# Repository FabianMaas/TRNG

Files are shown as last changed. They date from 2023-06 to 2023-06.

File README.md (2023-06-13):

<!-- markdown project template used: https://github.com/othneildrew/Best-README-Template -->

<!-- PROJECT SHIELDS -->
[][contributors-url]
[][stars-url]
[][issues-url]
[][license-url]

<!-- PROJECT LOGO -->
<br />
<div align="center">
  <a href="https://github.com/FabianMaas/TRNG">
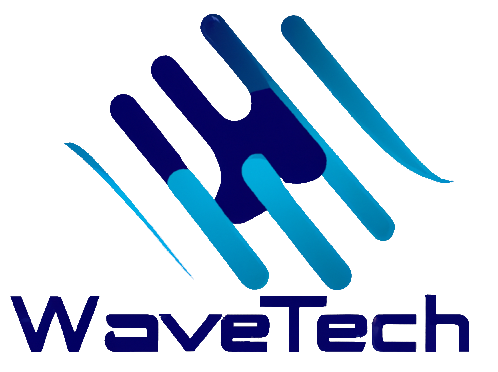
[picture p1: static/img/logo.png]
    
  </a>

<h3 align="center">True Random Number Generator</h3>

  <p align="center">
    An awesome TRNG based on a modified galton board.<br>
    Includes a REST API and a simple frontend.
    <br />
    <a href="https://github.com/FabianMaas/TRNG/tree/main/docs"><strong>Explore the docs »</strong></a>
    <br />
  </p>
</div>

---

<!-- TABLE OF CONTENTS -->
<details open>
  <summary>Table of Contents</summary>
  <ol>
    <li>
      <a href="#mag-about-the-project">About The Project</a>
      <ul>
        <li><a href="#gear-rest-api-endpoints">REST API</a></li>
        <li><a href="#construction_worker_man-built-with">Built With</a></li>
      </ul>
    </li>
    <li>
      <a href="#runner-getting-started">Getting Started</a>
      <ul>
        <li><a href="#pushpin-prerequisites">Prerequisites</a></li>
        <li><a href="#zap-installation">Installation</a></li>
        <li><a href="#white_check_mark-startup-of-the-rest-api">Startup of the api</a></li> 
      </ul>
    </li>
    <li>
      <a href="#camera_flash-screenshots">Screenshots</a>
      <ul>
        <li><a href="#starting-the-system">Starting the system</a></li>
        <li><a href="#generating-random-numbers">Generation</a></li>
        <li><a href="#exporting-the-generated-random-numbers">Export</a></li>
        <li><a href="#switching-to-dark-theme">Dark theme</a></li>
      </ul>
    </li>  
    <li><a href="#construction_worker_man-building-the-galton-board">Building the galton board</a></li>
    <li><a href="#scroll-license">License</a></li>
  </ol>
</details>

---

<!-- ABOUT THE PROJECT -->
## :mag: About The Project

| Bild 1 |  Bild 2 |
|:---:|:---:|

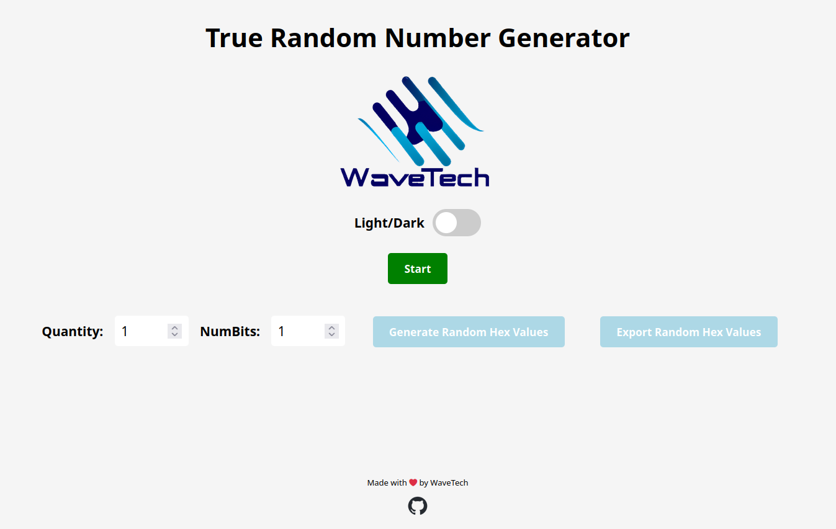
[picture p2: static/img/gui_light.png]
Bild 1


<!-- test 
<div style="display: flex; align-items: center;">
  <img src="static/img/gui_light.png" style="width: 49%;" alt="Beschreibung des Bildes">
  <img src="static/img/gui_dark.png" style="width: 50%; margin-top: auto; margin-bottom: auto;" alt="Beschreibung des Bildes">
</div> 
-->

<br>

The Galton Board is a Physical True Random Number Generator.<br>
The goal is to generate random numbers that can be used for cryptographic processes.<br>
It is based on a physical noise source and generates random numbers that fulfill the required PTG.2 standard of the
Federal Office for Information Security (BSI).<br>
<br> 
We offer a REST API interface or a web application with a user interface for operation.

<p align="right">(<a href="#readme-top">back to top</a>)</p>

---

## :gear: REST API endpoints
- `'/': Redirects to the TRNG page.`
- `'/trng': Renders the TRNG page.`
- `'/trng/randomNum/init': Initializes the TRNG system.`
- `'/trng/randomNum/shutdown': Shuts down the TRNG system.`
- `'/trng/randomNum/getRandom': Retrieves random bits from the database and converts them to HEX encoding.`
- `'/trng/getCount': Retrieves the count of stored random bits from the database.`
<br />
<a href="https://github.com/FabianMaas/TRNG/tree/main/docs/API"><strong>REST API Documentation »</strong></a>

---

### :construction_worker_man: Built With
* [][Python-url]
* [][Flask-url]
* [][SQLite-url]
* [][HTML5-url]
* [][CSS3-url]
* [][JavaScript-url]

<p align="right">(<a href="#readme-top">back to top</a>)</p>

---

<!-- GETTING STARTED -->
## :runner: Getting Started

To get a local copy of the project up and running follow these simple steps.

---

### :pushpin: Prerequisites

The project must run on a raspberry pi because it uses hardware components (gpio pins).<br>
For installing the dependencies you should use the latest version of pip.
* pip
  ```sh
  pip install --upgrade pip
  ```
---

### :zap: Installation

1. Clone the repo
   ```sh
   git clone https://github.com/FabianMaas/TRNG.git
   ```
2. Switch into the directory
   ```sh
   cd TRNG
   ```
3. Install PIP packages
   ```sh
   pip install -r requirements.txt
   ```

---

### :white_check_mark: Startup of the REST API
- ```sh
  python3 rest_api.py
  ```
<p align="right">(<a href="#readme-top">back to top</a>)</p>

---

## :camera_flash: Screenshots

### Starting the system

<p align="center">
  <img width="70%" height="70%" src="static/img/start_system_1.png">
</p>
<br>                                                            
<p align="center">
  <img width="70%" height="70%" src="static/img/start_system_2.png">
</p>

### Generating random numbers

<p align="center">
  <img width="70%" height="70%" src="static/img/generate_numbers_1.png">
</p>
<br>
<p align="center">
  <img width="70%" height="70%" src="static/img/generate_numbers_2.png">
</p>

### Exporting the generated random numbers

<p align="center">
  <img width="70%" height="70%" src="static/img/generate_numbers_3.png">
</p>

### Switching to dark theme

<p align="center">
  <img width="70%" height="70%" src="static/img/dark_theme_1.png">
</p>
<br>
<p align="center">
  <img width="70%" height="70%" src="static/img/dark_theme_2.png">
</p>

---

## :evergreen_tree: Project tree

```text
TRNG
├── LICENSE
├── README.md
├── docs
│   ├── API
│   │   └── ...
│   └── models
│       ├── README.md
│       ├── 3D
│       │   ├── GaltonBoard
│       │   │   ├── ...
│       │   │   └── ...
│       │   └── MarblePump
│       │       ├── ...
│       │       └── ...
│       └── lasercutter
│           ├── ...
│           └── ...
├── hardware
│   ├── gyroscope.py
│   ├── laser_sensor.py
│   └── stepper_engine.py
├── instance
│   └── TRNG.db
├── models
│   └── models.py
├── requirements.txt
├── rest_api.py
├── static
│   ├── css
│   │   └── main.css
│   ├── img
│   │   ├── ...
│   │   └── ...
│   └── js
│       ├── background.js
│       └── main.js
├── templates
│   └── index.html
└── tests
    └── test_suite.py

16 directories, 43 files
```
---

## :construction_worker_man: Building the galton board

- [Building instructions](https://github.com/FabianMaas/TRNG/blob/main/docs/models/README.md)
---

<!-- LICENSE -->
## :scroll: License

Distributed under the MIT License. See `LICENSE` for more information.

<p align="right">(<a href="#readme-top">back to top</a>)</p>

<!-- MARKDOWN LINKS & IMAGES -->
<!-- https://www.markdownguide.org/basic-syntax/#reference-style-links -->
[contributors-shield]: https://img.shields.io/github/contributors/FabianMaas/TRNG.svg?style=for-the-badge
[contributors-url]: https://github.com/FabianMaas/TRNG/graphs/contributors
[stars-shield]: https://img.shields.io/github/stars/FabianMaas/TRNG.svg?style=for-the-badge
[stars-url]: https://github.com/FabianMaas/TRNG/stargazers
[issues-shield]: https://img.shields.io/github/issues/FabianMaas/TRNG.svg?style=for-the-badge
[issues-url]: https://github.com/FabianMaas/TRNG/issues
[license-shield]: https://img.shields.io/github/license/FabianMaas/TRNG.svg?style=for-the-badge
[license-url]: https://github.com/FabianMaas/TRNG/blob/master/LICENSE
[gui-light]: static/img/gui_light.png
[gui-dark]: static/img/gui_dark.png
[galton-board]: static/img/Galton_Board.png
[Python]: https://img.shields.io/badge/python-3670A0?style=for-the-badge&logo=python&logoColor=ffdd54
[Python-url]: https://www.python.org/
[Flask]: https://img.shields.io/badge/flask-%23000.svg?style=for-the-badge&logo=flask&logoColor=white
[Flask-url]: https://flask.palletsprojects.com
[SQLite]: https://img.shields.io/badge/sqlite-%2307405e.svg?style=for-the-badge&logo=sqlite&logoColor=white
[SQLite-url]: https://www.sqlite.org
[HTML5]: https://img.shields.io/badge/html5-%23E34F26.svg?style=for-the-badge&logo=html5&logoColor=white
[HTML5-url]: https://www.w3.org/standards/webdesign/htmlcss
[CSS3]: https://img.shields.io/badge/css3-%231572B6.svg?style=for-the-badge&logo=css3&logoColor=white
[CSS3-url]: https://www.w3.org/standards/webdesign/htmlcss
[JavaScript]: https://img.shields.io/badge/javascript-%23323330.svg?style=for-the-badge&logo=javascript&logoColor=%23F7DF1E
[JavaScript-url]: https://www.ecma-international.org/publications-and-standards/standards/ecma-262/

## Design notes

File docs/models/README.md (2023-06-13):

# Building instructions
-   [Galton Board](#galton-board)
-   [Preparation](#preparation)
    -   [Tools](#tools)
    -   [Material](#material)
    -   [Prior knowledge](#prior-knowledge)
-   [Building instructions](#building-instructions)
    -   [Galton Board](#galton-board)
	    - [Base frame](#base-frame)
	    -  [Box](#box)
	    - [Slide](#slide)
	- [Marble lift](#marble-lift)
	- [Stepper motor](#stepper-motor)
	- [RasberryPi](#rasberrypi)
		- [RasberryPi holder](#rasberrypi-holder)
		- [Circuit board](#circuit-board)
		- [Sensor system](#sensor-system)
-   [Improvement ideas](#improvement-ideas)
---
## Galton Board
Our variation of a galton board uses only two compartments instead of many. Every pin inside a galton board has a 50% chance to be left or right. We use this uniform distribution to generate binary-valued random numbers. Our board has two stages with one pin per stage. Each compartment on each stage produces a bit, either a zero or a one. We use plastic marbles which run trough the system and interrupt laser which are pointed onto sensors. In the end they will get pumped up to the top again with a piston lift.

<p align="center">
  
</p>

## Preparation

### Tools
- Laser cutter
- 3D printer
- Superglue
- Wood glue
- Soldering iron
- Sandpaper and file
- Screwdriver or drill
- Screws
- Pliers

### Material

<table>
    <tr>
      <th>Material</th>
      <th>Count
      <th>Measures</th>
    </tr>
  <tbody>
    <tr>
      <td>MDF</td>
      <td>1x</td>
      <td>~605 x 550mm</td>
    </tr>
    <tr>
      <td>ABS</td>
      <td>1x</td>
      <td>~195g or 27.9m</td>
    </tr>
    <tr>
      <td>PLA</td>
      <td>1x</td>
      <td>~4g</td>
    </tr>
    <tr>
      <td>Acryl plate</td>
      <td>1x</td>
      <td>~231 x 306mm</td>
    </tr>
    <tr>
      <td>Metal rod</td>
      <td>2x</td>
      <td>21 x 5(diameter)mm</td>
    </tr>
    <tr>
      <td>RasberryPi</td>
      <td>1x</td>
      <td>Model B Version 3, with offical power supply</td>
    </tr>
    <tr>
      <td>Stepper motor</td>
      <td>1x</td>
      <td>Power supply 12V, 1.5A</td>
    </tr> 
    <tr>
      <td>Laser</td>
      <td>4x</td>
      <td>5mW; 650nm</td>
    </tr>
    <tr>
      <td>Photodiodes</td>
      <td>4x</td>
      <td>32 x 14mm; 3.3V-5V operating voltage</td>
    </tr>
	  <tr>
      <td>Jumper Cables</td>
      <td>40x</td>
      <td>16x blue; 16x red; 8x black</td>
    </tr>
    <tr>
      <td>Tube</td>
      <td>1x</td>
      <td>15mm diameter inside; 18mm diameter outside; 45cm length</td>
    </tr>
    <tr>
      <td>Height-adjustable feet</td>
      <td>4x</td>
      <td>50 x 50mm</td>
    </tr>
    <tr>
      <td>Marbles</td>
      <td>40x</td>
      <td>Acryl; 14mm</td>
    </tr>
    
  </tbody>
</table>

### Prior knowledge
The following instructions require previous knowledge of how to use the laser cutter and
the 3D printer as well as experience in soldering.
Basic manual skills are recommended.

---
## Building instructions
### Galton Board

The first thing to do is to cut the following SVG files. The materials used for this project are MDF and acrylic, with MDF being the primary material. Both materials have a thickness of 3mm and should be cut to the exact dimensions specified in the sketches.

Make sure that the acrylic that you use is transparent. You can also remove the logo or add your own logo.
<br>
The following SVG files should be printed on MDF:

- Prototype.svg
- UnderBox.svg
- Slide.svg
- Slide2AndTop.svg

The SVG file for the acrylic material is:

- Glas.svg

After cutting all the components, you will have the following parts:
<details open>
<summary>All parts:</summary>
<br>





</details>

<br>

#### Base Frame

Arrange the parts as shown in the picture, ensuring everything is easily accessible. Glue the prongs together on both sides using wood glue. Repeat this step for each side. Depending on the color of the MDF, you can decide which side should face the front.

<details open>
<summary>The procedure is as follows:</summary>
<br>



</details>
<br>
The acrylic plate from the Glass.svg file serves as the lid for the Galton board. However, this is the final step after everything else has been installed on the board.

**Tip**: The acrylic board and the MDF should not be glued together. This allows you to remove the board whenever necessary for maintenance. Additionally, acrylic and MDF do not bind well when glued.
<br>
Next, we move to the end piece at the bottom, where the marbles land and roll out. This step is straightforward.

<details open>
<summary>The process is as follows:</summary>
<br>


</details>

Simply glue the pieces on top of each other, allowing time for the wood glue to dry between layers. Try to ensure the layers are glued as straight as possible.

**Tip:** If there are any unevenness in the end piece, you can correct it by sanding it straight.

At the end of both processes, you can combine them together. The combined result should look like this:
<details open>
<summary>Combination:</summary>
<br>

</details>
<br>

#### Box
Now we come to the building instructions for the box located beneath the Galton board. The process is similar to building the Galton board. 

<details open>
<summary>The process is as follows:</summary>
<br>



</details>

However, note that the lid should not be glued down yet. This will allow you to lay the cables later. The box is already stable enough with just one side glued.

The box provides a way to hide the large number of cables as much as possible. It features holes on the sides through which side cables can be neatly routed underneath the box, resulting in a cleaner appearance. The same principle applies to the back of the Galton board, ensuring a tidy and organized setup.

<details open>
<summary>Cable management</summary>
<br>


</details>

<br>

#### Slide
Finally, we move on to the slide, which connects the board with the lift. A file is still needed for this step.

<details open>
<summary>Please refer to the following pictures:</summary>
<br>



</details>

With all four parts, it doesn't need to be filed very steeply, but it is important that it has a straight angle. 

Once that is done, you can assemble these parts together, resulting in the following configuration:

<details open>
<summary>Configuration:</summary>
<br>

</details>

After assembling the slide, you can also glue the "funnel" at the end of the slide. It should look something like this:

<details open>
<summary>Configuration:</summary>
<br>

</details>

**Tip:** Ensure that the funnel is tight enough at the end to accommodate exactly one marble on the back wall.

<br>
At the end, when everything is glued together, you can also insert the pieces from the 3D scanner into the cutouts on the boards. The picture allows you to clearly see which item should go where, making it relatively simple to put everything together. It is recommended to use superglue to securely attach all the 3D items in place.

The following STL files should be printed with ABS:

- Hopper_Part_Level1.stl
- Hopper_Part_Level2.stl
- Laser_Diode_Mount.stl
- Photoresistor_Mount.stl

<details open>
<summary>Configuration:</summary>
<br>

</details>

Additionally, print the following files to connect the galton board with the box unterneath:

- Corner_Marble_Exit.stl
- Corner.stl

The normal corner is needed three times and the corner at the marble exit only once.

<details open>
<summary>Corner:</summary>
<br>

</details>

<br>

### Marble lift
To bring the marbles back up to the top of the galton board we use a marble lift. It uses a piston system to stack the marbles on top of each other. First you want to make sure that you have everything in front of you. The following picture shows all the parts you need.  

To do this, print the stl.-files of the Marble Pump section with the material ABS.
Leave out the following file: Connector_Stepperengine.stl

<details open>
<summary>All parts:</summary>
<br>

</details>

There might be some parts with support structures, which were added by the 3D printer. You must remove them to be able to assemble the parts. In the pictures below you can see the support structure of the sliding part. The first picture shows the part with the support structure and the second shows it without.

<details open>
<summary>Support structre:</summary>
<br>


</details>

The next step will be the trickiest, because we need to get the crankshaft in place. In the following there will be series of pictures which fit this expiration:
1. These are all the parts you need for the crankshaft (Pictures 1, 2 and 3)
2. In the fourth picture you can see how the cranshaft will be stuck together inside the sliding part. As you can see you need the connector tube and two of the angled square sticks. The short side of the sticks will go inside the connector tube. (Don't put them in yet!!! This is just for demonstration)
3. The sliding part will sit inside of the part with the two holes, we call it housing. Before you place it there (as in picutre one), we must put the connector tube inside of it (as in picture three).

<details open>
<summary>Assembling the crankshaft: Part 1:</summary>
<br>




</details>
<br>

4. The next few steps are easier with a second person that helps with the process.
5. You must fit the two angled square sticks through the holes on each side of the housing, so that the angle is inside the housing. The first picture below shows it.
6. Now you must manage to stick one stick inside the connector tube.
7. The second person must now pull both sides of the housing away from each other, like in the second picture below.
8. While the second person is pulling it apart, you must connect the other stick to the connector pipe.
9. If the sticks and the pipe are stuck tight togther you must put the crankshaft brackets, as you can see on the last two pictures, on top of each crankshaft side.  
10. The assembling of the crankshaft is done.

<details open>
<summary>Assembling the crankshaft: Part 2:</summary>
<br>




</details>
<br>

There are three more steps until the marble lift is done. First you must insert the piston, so that the open part of the piston fits onto the crankshaft tube inside of the sliding part. You can drop the piston from the top tough one of the holes of the housing. The second step is to slide the whole thing into the base, as you see in the first picture below. And finally put the connection for the hose on. There should be 4 pins which fit inside into the 4 holes on top of the lift. These are the connection parts between the lift itself and the hose. Now you can place the hose holder part on top of the lift aligned with the 4 pins.

<details open>
<summary>Connecting the hose:</summary>
<br>



</details>

To integrate the marble pump to the rest of the system, connect the tube with the top of the marble pump.
Print the file Tube_Mount.stl to attach the upper part of the tube with the top of the Galton Board.

**Tip:** The correct Tube_Mount-stl file is in the section Galton Board.

To close the loop of the marbles, add the slide between the marble exit of the Galton Board and the open entry of the marble pump.

<details open>
<summary>Marble pump attachment:</summary>
<br>


</details>

<br>

### Stepper motor
The stepper motor must be placed on one of the two sides of the lift. You must install the connector tube for the connection between the stepper motor and the lift. Just press the end of the crankshaft, which sticks out of the side of the lift, into the connector tube (the green part in the picture). You must do the same with the shaft of the stepper motor. If it fits tight, you need to make sure that both parts, the motor and the lift, are placed perfecly and then should be mounted to the base.

The green part is printed with PLA. Use the file Connector_Stepperengine.stl to print the component.

<details open>
<summary>Connecting the stepper motor</summary>
<br>

</details>
<br>

### RasberryPi
This section provides instructions on how to connect the components that come with the Raspberry Pi. A bracket is used to stabilize the Raspberry Pi and prevent unnecessary movement or wobbling. 

Additionally, a circuit board is provided to ensure the proper connection of individual parts.

#### RasberryPi holder

Use the following file to print the holder of the Raspberry Pi. Add it next to the stepper motor and insert the Pi into its holding.

- RaPi_Holder.stl

<details open>
<summary>RaspberryPi holder:</summary>
<br>


</details>

<br>

#### Circuit board
This chapter describes our self engineered circuit diagram, please refer to the picture below if you intent to use an own circuit board aswell. An example of how to wire the circuit diagram would look like this:

<details open>
<summary>Example:</summary>
<br>


</details>
<br>

#### Sensor system
In this step, the sensors are installed.
The two brackets for the laserdiodes are filled with two laserdiodes each bracket and are
glued into the middle of the Galton Board. The four photodiodes are clipped into their
designated sockets and plugged into the sides of the Galton board.
For the next step, both the lasers and the photodiodes must be connected to the power supply.
The photodiodes have an indicator light that lights up when a laser signal is received. Now
the lasers and photodiodes have to be aligned with each other. The lasers inside and the
photodiodes with their brackets are moved slightly until the control lamp lights up. As soon as all four lights are lit, the brackets are glued in this position to the outer side of the Galton Board and the lasers are held in their position on the inside.

<details open>
<summary>Sensor system:</summary>
<br>


</details>

The picture below shows an aligned (below) and an unaligned (above) laser. For the top photodiode, only the power indicator light is on, but the laser signal light is off.
The acrylic glass can be added to the system. It is important that the glass is not glued or
fixed to the rest of the Galton Board.

<details open>
<summary>Laser alignment:</summary>
<br>

</details>
<br>

## Improvement ideas
Since the project was developed unter the conditions of a prototype, the existing concept can be improved and expanded.

For example, a gyroscope can be used for better taring. This would attached to the Galton Board at a suitable location, aligned accordingly and integrated with this data in the code.

Another improvement can be reached by using more precise tools to cut or print the components. But this improvement needs additional resources.

Additionally, the Galton Board can be duplicated and arranged in cascade to increase the performance.

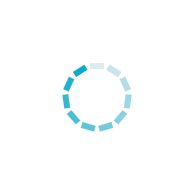
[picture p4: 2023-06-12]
static/img/spinner.gif

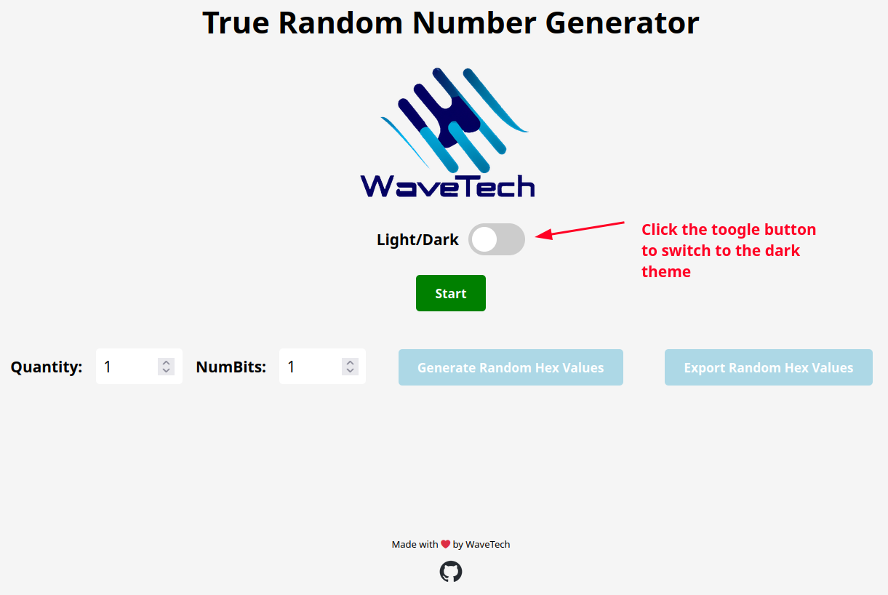
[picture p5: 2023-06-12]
static/img/dark_theme_1.png

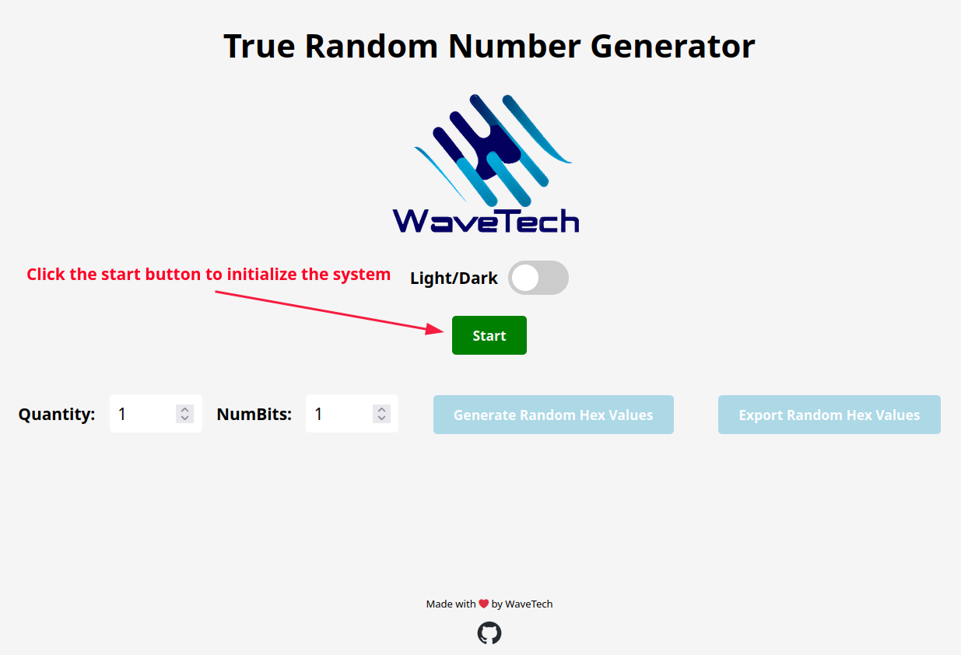
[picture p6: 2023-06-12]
static/img/start_system_1.png

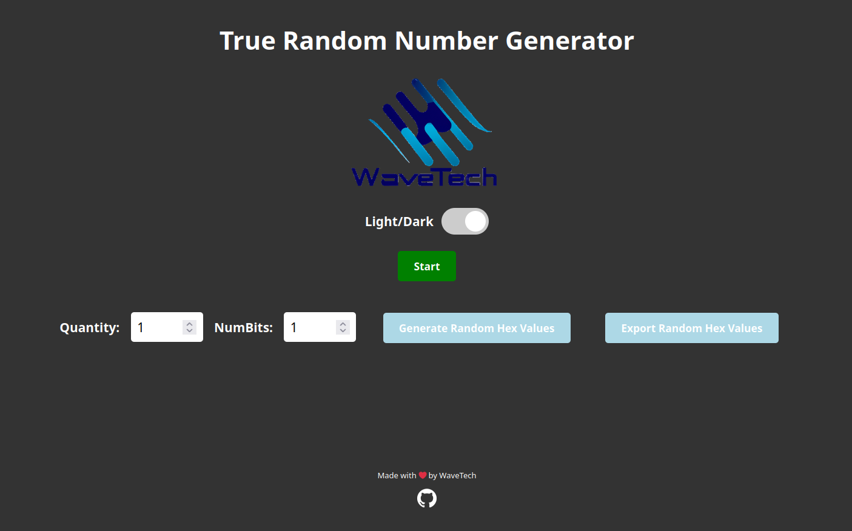
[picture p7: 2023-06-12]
static/img/gui_dark.png

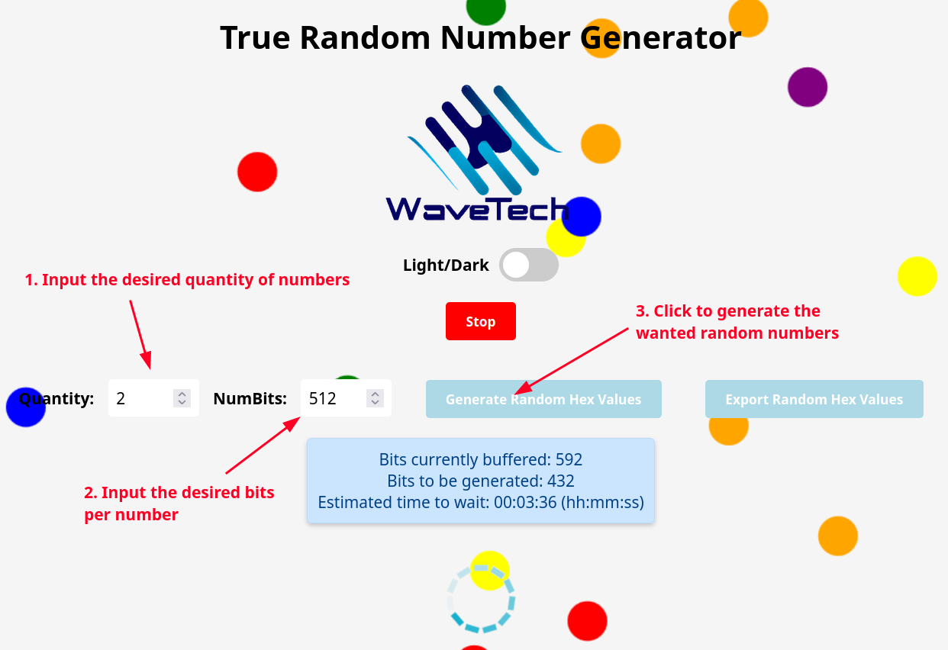
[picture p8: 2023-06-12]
static/img/generate_numbers_1.png

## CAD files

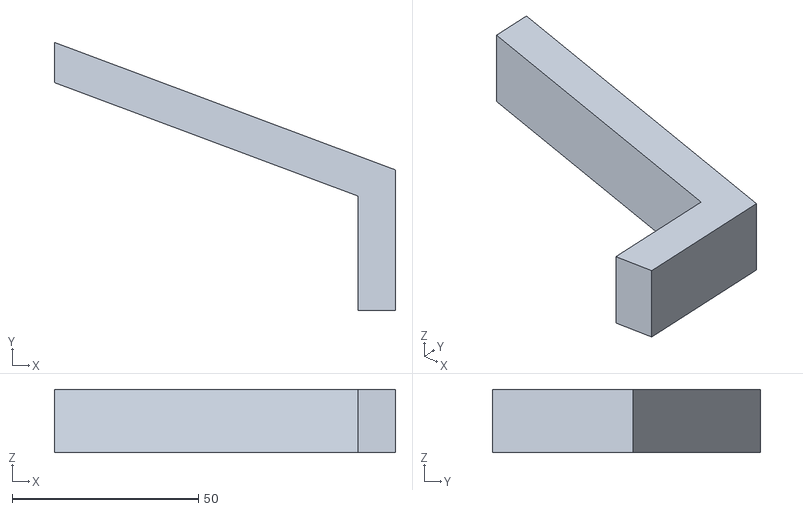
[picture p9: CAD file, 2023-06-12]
docs/models/3D/GaltonBoard/Hopper_Part_Level_1.stl
91.5 x 72.0 x 17.0

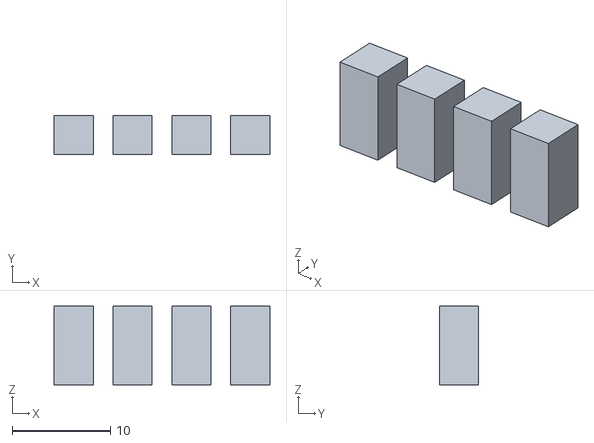
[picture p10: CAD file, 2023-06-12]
docs/models/3D/MarblePump/Pins.stl
22.0 x 4.00 x 8.00

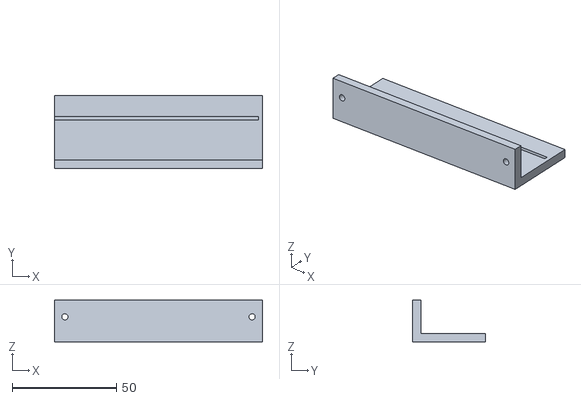
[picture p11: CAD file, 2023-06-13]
docs/models/3D/RaPi_Holder.stl
100.0 x 35.0 x 20.0

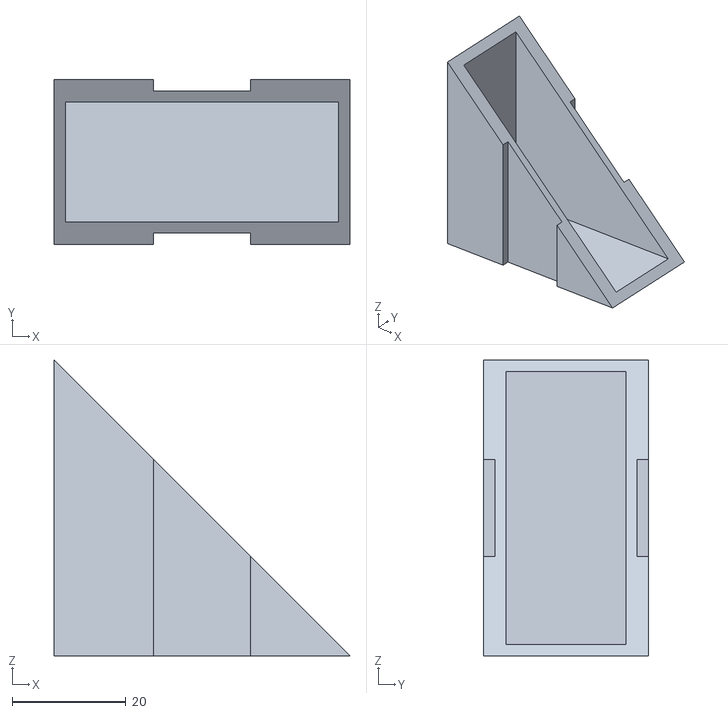
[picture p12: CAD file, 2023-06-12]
docs/models/3D/GaltonBoard/Corner.stl
52.0 x 29.0 x 52.0

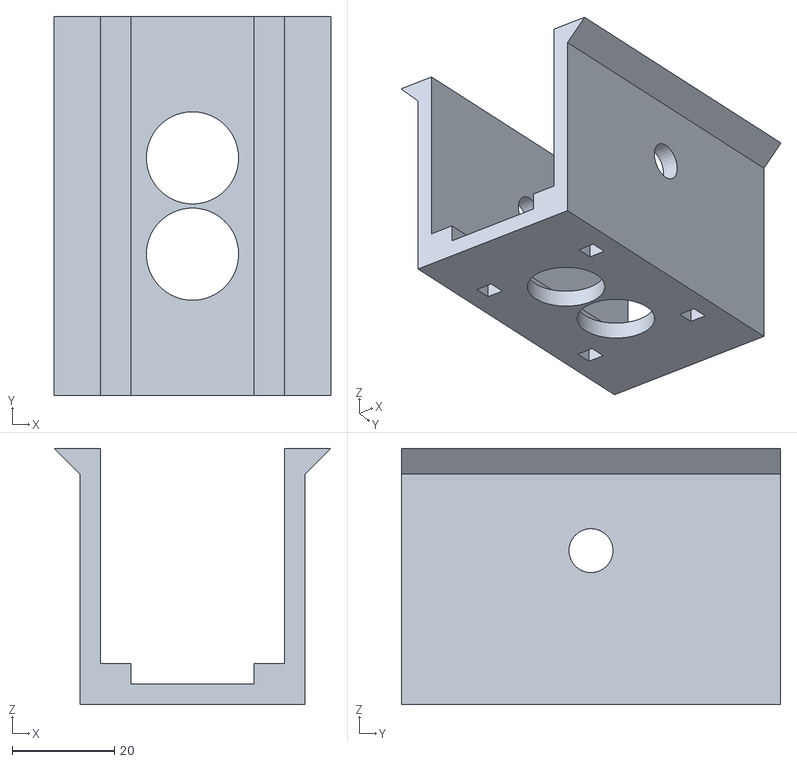
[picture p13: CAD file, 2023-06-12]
docs/models/3D/MarblePump/Housing.stl
54.0 x 74.0 x 50.0

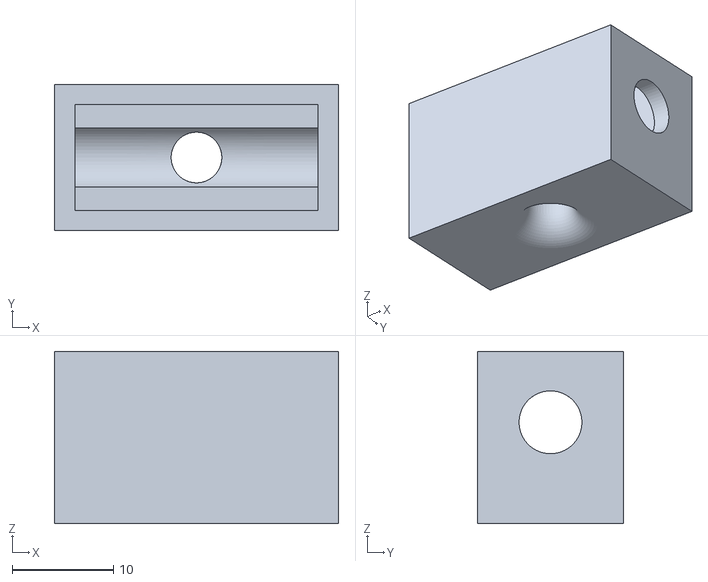
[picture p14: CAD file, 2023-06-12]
docs/models/3D/GaltonBoard/Laser_Diode_Mount.stl
28.0 x 14.4 x 17.0

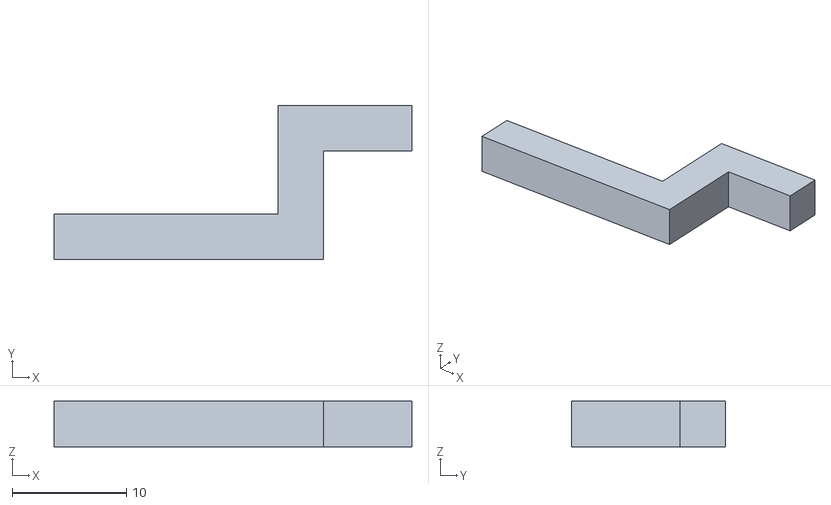
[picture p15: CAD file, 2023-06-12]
docs/models/3D/MarblePump/Crankshaft.stl
31.3 x 13.5 x 4.00

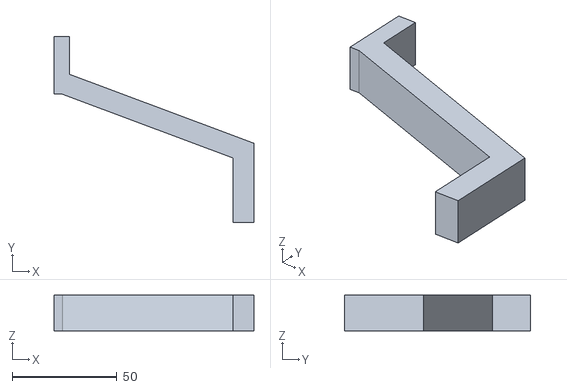
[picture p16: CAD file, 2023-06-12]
docs/models/3D/GaltonBoard/Hopper_ Part_Level_2.stl
95.5 x 88.7 x 17.0

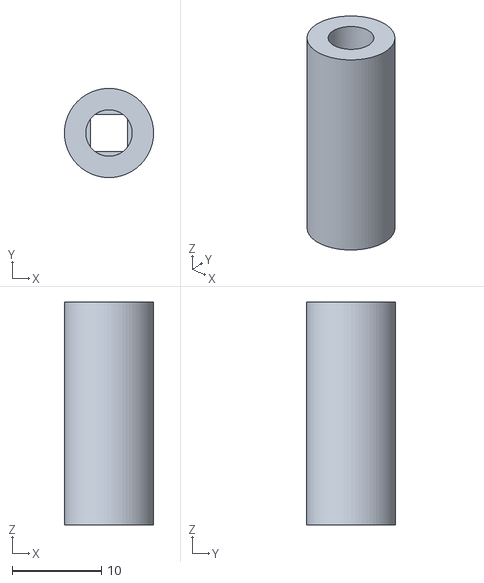
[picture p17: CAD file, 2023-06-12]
docs/models/3D/MarblePump/Connector_Stepperengine.stl
10.0 x 9.99 x 25.0

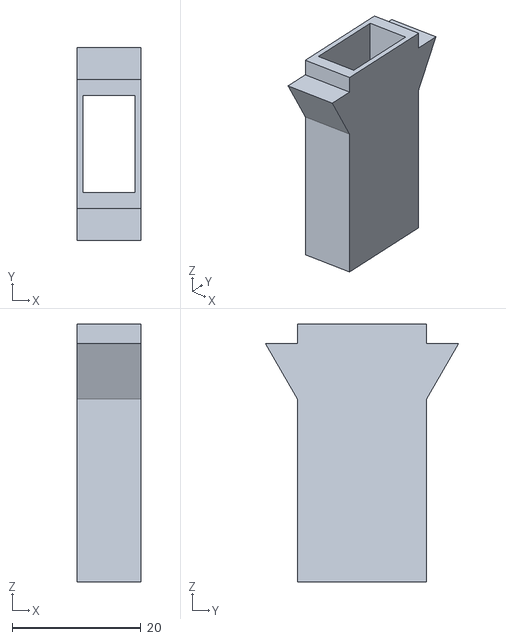
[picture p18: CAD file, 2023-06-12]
docs/models/3D/GaltonBoard/Photoresistor_Mount.stl
10.0 x 30.0 x 40.0

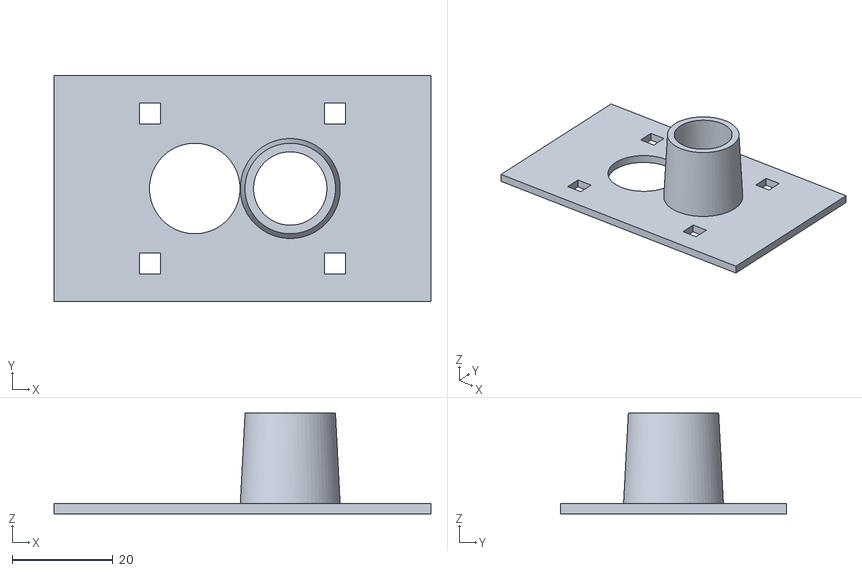
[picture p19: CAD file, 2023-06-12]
docs/models/3D/MarblePump/Tube_Mount.stl
75.0 x 45.0 x 20.0

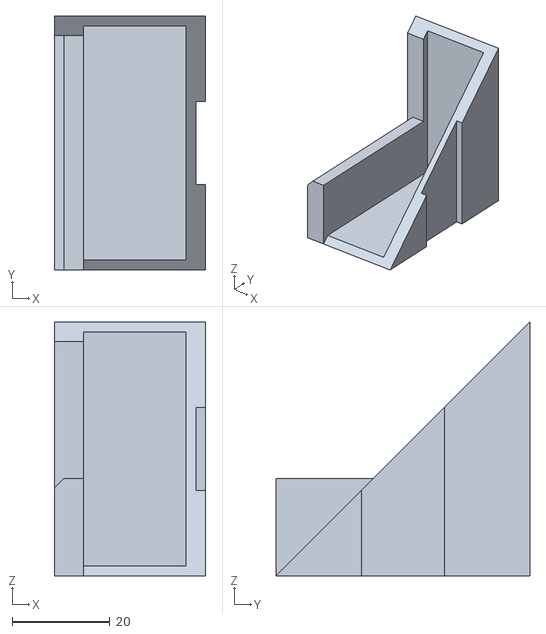
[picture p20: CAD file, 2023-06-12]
docs/models/3D/GaltonBoard/Corner_Marble_ Exit.stl
31.0 x 52.0 x 52.0

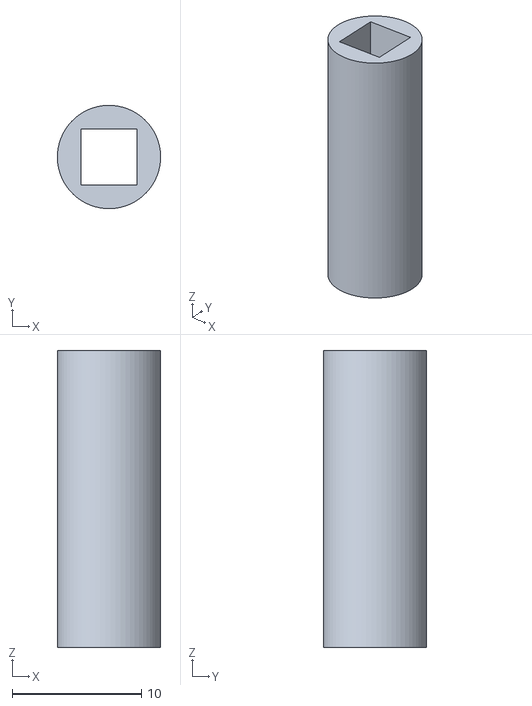
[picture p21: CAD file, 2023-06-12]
docs/models/3D/MarblePump/Journal_Crankshaft.stl
8.00 x 8.00 x 23.0

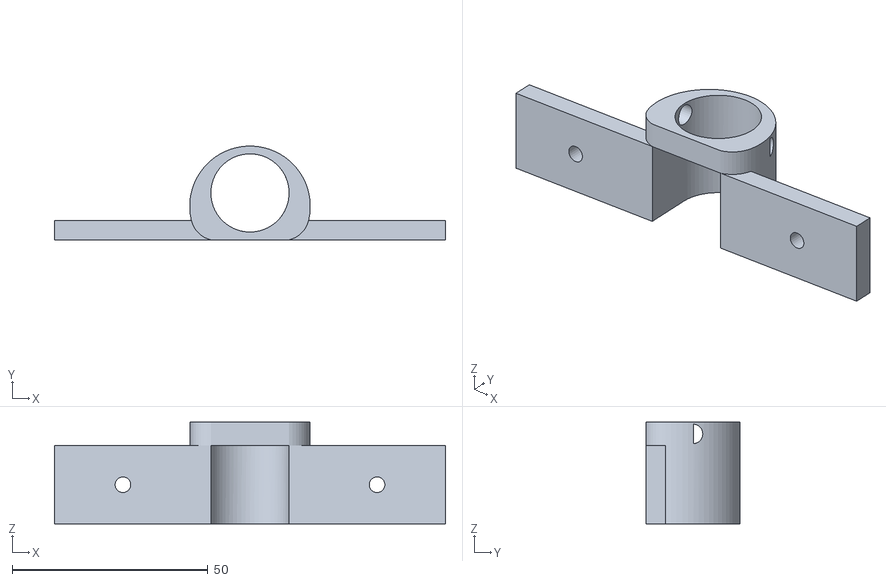
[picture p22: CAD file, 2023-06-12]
docs/models/3D/GaltonBoard/Tube_Mount.stl
100.0 x 24.0 x 26.0

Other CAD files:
docs/models/3D/MarblePump/Base.stl
docs/models/3D/MarblePump/Piston.stl
docs/models/3D/MarblePump/Slide.stl
docs/models/3D/MarblePump/Cap_Crankshaft.stl

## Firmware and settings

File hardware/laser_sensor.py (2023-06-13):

"""
This file provides the LaserSensor class for controlling a laser sensor using Raspberry Pi GPIO pins.

The LaserSensor class allows reading sensor data, writing data to a database, and managing event-based callbacks for sensor events. 
It utilizes the RPi.GPIO library for GPIO pin manipulation, the time library for delays and timing calculations, 
the datetime library for time-based operations, the random library for generating random bits, 
the models module for interacting with the database, and the multiprocessing library for event handling.

Imports:
- datetime: Provides classes for manipulating dates and times.
- models: Contains the data models for the application.
- multiprocessing: Supports the execution of multiple processes in parallel.
- os: Provides a way of using operating system-dependent functionality.
- random: Generates random numbers and provides random selection functionality.
- RPi.GPIO: Allows control of Raspberry Pi GPIO pins.
- time: Provides various time-related functions.

Classes:
- LaserSensor: Controls a laser sensor and manages data reading and writing.
"""


import datetime
import models.models as models
import multiprocessing
import os
import random
import RPi.GPIO as GPIO
import time


class LaserSensor:
    """
    Represents a laser sensor controlled using Raspberry Pi GPIO pins.\n
    Attributes:
    - __queue_top (multiprocessing.Queue): A queue for storing data from the top laser sensor.
    - __queue_bottom (multiprocessing.Queue): A queue for storing data from the bottom laser sensor.
    - __top_down (bool): A flag indicating if the top laser sensor is currently down.
    - __bottom_down (bool): A flag indicating if the bottom laser sensor is currently down.
    - __list_top (list): A list for tracking data from the top laser sensor.
    - __list_bottom (list): A list for tracking data from the bottom laser sensor.\n
    Methods:
    - start(self): Starts the sensor and begins monitoring the queues.
    - write_to_db(self, rest_api, error_event: multiprocessing.Event): Constantly checks the data queues and writes to the database when the queue reaches 8 bits.
    - __loop(self): Main loop for monitoring the laser sensors.
    - __callback_func1(self, channel): Callback function for handling events from the first laser sensor.
    - __callback_func2(self, channel): Callback function for handling events from the second laser sensor.
    - __callback_func3(self, channel): Callback function for handling events from the third laser sensor.
    - __callback_func4(self, channel): Callback function for handling events from the fourth laser sensor.
    - __add_time_based_random_bits(self, queue): Adds time-based random bits to the specified queue.
    """
    __queue_top = multiprocessing.Queue()
    __queue_bottom = multiprocessing.Queue()
    __top_down = multiprocessing.Event()
    __bottom_down = multiprocessing.Event()
    __list_top = []
    __list_bottom = []


    def start(self):
        """
        Starts the laser sensor and begins monitoring the queues.\n
        Parameters:
        - self: The current instance of the class.
        """
        try:
            self.__loop()
        except Exception as e:
            print("EXCEPTION from queue loop: " + str(e))
            pass


    def write_to_db(self, rest_api, error_event: multiprocessing.Event):
        """
        Checks the data queues constantly and writes to the db,
        if the queue reaches 8 Bit.\n
        Parameters:
        - self: The current instance of the class.
        - rest_api is an flask instance object.
        - error_event is an object of the type Event from multiprocessing library.
        """
        last_executed_time = datetime.datetime.now()
        while True:
            current_time = datetime.datetime.now()
            difference = current_time - last_executed_time
            datetime.timedelta(0, 4, 316543)
            
            """
            if no bits going to be generated within 15 seconds an error object will be set to true.
            The error object is needed to let the engine turn backwards to fix stuck marbles.
            """
            if difference.total_seconds() > 15:
                error_event.set()               
                last_executed_time = datetime.datetime.now()
            

            print("Bottom queue size: " + str(self.__queue_bottom.qsize()))
            print("Top queue size: " + str(self.__queue_top.qsize()))
            #print("Bottom down: " + str(self.__bottom_down.is_set()))
            #print("Top down: " + str(self.__top_down.is_set()))


            tmp_rand_arr = []

            if ((self.__queue_top.qsize() >= 8 and not self.__top_down.is_set()) or (self.__queue_bottom.qsize() >= 8 and not self.__bottom_down.is_set())):
                tmp_rand_arr.clear()

                if (not self.__bottom_down.is_set()) and self.__queue_bottom.qsize() > self.__queue_top.qsize():
                    print("first if---------------------------------")
                    count = 0
                    while (not self.__bottom_down.is_set()) and count < 8:
                        try:
                            tmp = self.__queue_bottom.get()
                            tmp_rand_arr.append(tmp)
                            self.__list_bottom.append(tmp)

                            if len(self.__list_bottom) >= 32:
                                print("DEBUG bottom-list: " + str(self.__list_bottom))
                                if self.__list_bottom.count(0) > 30 or self.__list_bottom.count(1) > 30:
                                    self.__bottom_down.set() 
                                    continue

                                self.__list_bottom.pop(0)

                            count += 1
                        except Exception as e:
                            print("EXCEPTION from top queue write: " + str(e))
                            pass    
                elif (not self.__top_down.is_set()) and self.__queue_top.qsize() > self.__queue_bottom.qsize():
                    print("second if---------------------------------")
                    count = 0
                    while (not self.__top_down.is_set()) and count < 8:
                        try:
                            tmp = self.__queue_top.get()
                            tmp_rand_arr.append(tmp)
                            self.__list_top.append(tmp)
                            
                            if len(self.__list_top) >= 32:
                                print("DEBUG top-list: " + str(self.__list_top))
                                if self.__list_top.count(0) > 30 or self.__list_top.count(1) > 30:
                                    self.__top_down.set()
                                    continue

                                self.__list_top.pop(0)
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

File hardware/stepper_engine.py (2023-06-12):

"""
This file controls a stepper motor using Raspberry Pi GPIO pins.

It provides the StepperEngine class, which allows starting, stopping, and controlling the motor's rotation. 
The class utilizes the RPi.GPIO library for GPIO pin manipulation and the multiprocessing library for event handling.

Imports:
- multiprocessing.Event: Provides event-based communication between processes.
- RPi.GPIO: Provides access to the Raspberry Pi's GPIO pins for controlling the motor.
- time: Provides sleep functionality for controlling the delay between motor steps.
- warnings: Allows filtering and ignoring runtime warnings.

Classes:
- StepperEngine: Controls the stepper motor and handles its rotation.
"""


from multiprocessing import Event
import RPi.GPIO as GPIO
from time import sleep
import warnings


class StepperEngine:
	"""
	The StepperEngine class controls a stepper motor using Raspberry Pi GPIO pins.\n
	Attributes:
	- __DIR (int): The GPIO pin number for the direction of rotation.
	- __STEP (int): The GPIO pin number for the step signal.
	- __CW (int): The value representing clockwise rotation.
	- __step_count (int): The number of steps per revolution.
	- __delay (float): The delay between steps, controlling the turning speed.\n
	Methods:
	- start(self, error_event: Event): Starts the engine and runs it until termination.
 	- reset(self): Resets the engine's operation.
	- __setup(self): Sets up the GPIO pins and their behavior.
	- __loop(self): Executes a loop that continuously rotates the motor in a forward direction.
	- __reverse_engine(self, rounds): Spins the engine backwards for a specified number of rounds.
	"""
	__DIR = 5   # Direction GPIO Pin
	__STEP = 6  # Step GPIO Pin
	__CW = 0     # Clockwise Rotation
	#CCW = 1    # Counterclockwise Rotation (not in use)
	__step_count = 1600   # Steps per Revolution
	__delay = .0001	# Turning speed


	def start(self, error_event: Event):
		"""
		Starts the whole process with setting up the GPIO Pins and
		runs the engine until the engine process gets terminated.\n
		Parameters:
  		- self: The current instance of the class.
		- error_event: a object of the type Event from multiprocessing library
		"""
		warnings.filterwarnings("ignore", category=RuntimeWarning)
		self.__error_event = error_event
		
		try:
			self.__reset()
		except Exception as e:
			print("EXCEPTION from engine reset: " + str(e))
			pass
		try:
			self.__setup()
		except Exception as e:
			print("EXCEPTION from engine setup: " + str(e))
			pass
		try:
			self.__loop()
		except Exception as e:
			print("EXCEPTION from engine loop: " + str(e))
			pass


	def __reset(self):
		"""
		The endless run of the engine will be reseted with a call of this function.\n
  		Parameters:
		- self: The current instance of the class.
		"""
		try:
			GPIO.output(self.__STEP, GPIO.LOW)
			GPIO.cleanup()
		except:
			pass


	def __setup(self):
		"""
		Sets up the physical location of the GPIO pins
		and their behavior.\n
		Parameters:
		- self: The current instance of the class.
		"""
		GPIO.setmode(GPIO.BCM)
		GPIO.setup(self.__DIR, GPIO.OUT)
		GPIO.setup(self.__STEP, GPIO.OUT)
		GPIO.output(self.__DIR, self.__CW)


	def __loop(self):
		"""
		Executes a loop that continuously rotates a motor in a forward direction,
		while monitoring for any error events. If an error event is detected, the motor
		is reversed for a specified duration and the error event is cleared.\n
		Parameters:
		- self: The current instance of the class.
		"""
		while True:
			if self.__error_event.is_set():
				self.__reverse_engine(5)
				self.__error_event.clear()
			for x in range(self.__step_count):
					GPIO.output(self.__STEP, GPIO.HIGH)
					sleep(self.__delay)
					GPIO.output(self.__STEP, GPIO.LOW)
					sleep(self.__delay)


	def __reverse_engine(self, rounds):
		"""
		If there are marbles stuck in front of the lift
		call this function to let the engine spin backwards for x rounds.\n
		Parameters:
  		- self: The current instance of the class.
		- rounds: An integer to tell how many rounds the engine will be spinning backwards.
		"""
		self.__reset()
		self.__CW = 1
		self.__setup()
		for x in range(rounds):
			for y in range(self.__step_count):
					GPIO.output(self.__STEP, GPIO.HIGH)
					sleep(self.__delay)
					GPIO.output(self.__STEP, GPIO.LOW)
					sleep(self.__delay)
		self.__reset()
		self.__CW = 0
		self.__setup()

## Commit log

2023-05-11 added stepperengine and lasersensor code
2023-05-15 thread fix
2023-05-16 Pokertest fixed & Stepperengine improved
2023-05-21 engine loop now checks for error_event instead of creating an additional watcher process and fixed some naming conventions
    [laser_sensor.py, stepper_engine.py]
2023-05-21 added top_down and bottom_down to disable laser in loop if only 0's or 1's are read from the associated queue
2023-05-22 reset time if error_event is set
    [laser_sensor.py]
2023-05-22 Debug prints
2023-05-22 int string convert problem solved
    [laser_sensor.py]
2023-05-22 fix for consecutive number variable
    [laser_sensor.py]
2023-05-22 fix again error event
    [stepper_engine.py]
2023-05-22 fix test again error event
    [stepper_engine.py]
2023-05-23 added gyroscope code
2023-05-23 besser postion of debug print
2023-05-23 comment debug prints
2023-05-25 switched total failure check
    [laser_sensor.py]
2023-05-25 Debug print for new implementation
2023-05-25 switch form size() to len()
2023-05-30 STL-3D Print
    [Base_No_Motor.stl, Cap_Crankshaft.stl, Crankshaft.stl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]
2023-05-31 new folders for 3D models
    [Base_No_Motor.stl, Cap_Crankshaft.stl, Crankshaft.stl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]
2023-05-31 better structure for docs
    [Base_No_Motor.stl, Cap_Crankshaft.stl, Crankshaft.stl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]
2023-05-31 pull after merge
    [Base_No_Motor.stl, Cap_Crankshaft.stl, Crankshaft.stl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]
2023-05-31 Create lasercutter
2023-05-31 Create Prototype
2023-05-31 adding stl files after merge problems.
    [Base_No_Motor.stl, Cap_Crankshaft.stl, Crankshaft.stl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]
2023-06-01 Debug for the queues
    [Trichter-Ebene1.stl, Trichter-Ebene2.stl]
2023-06-01 Funnel already exists under funnel
    [Trichter-Ebene1.stl, Trichter-Ebene2.stl]
2023-06-01 fix endless loop 2
    [laser_sensor.py]
2023-06-01 total failure wasn't running
    [laser_sensor.py]
2023-06-05 added light/dark theme toggle button and structured main.css
2023-06-06 fixed total failure test
    [laser_sensor.py]
2023-06-06 fix because of wrong variable
    [laser_sensor.py]
2023-06-12 changed all 3D models
    [Base.stl, Cap_Crankshaft.stl, Connector_Stepperengine.stl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]
2023-06-12 added galton board picture to building instructions
2023-06-12 Adding text and adding jumper cables to table
2023-06-13 Adding stepper motor instructions
2023-06-13 add version 3 to Raspberry Pi in table
2023-06-13 add jumper cables data
2023-06-13 pic galton board
2023-06-13 picture final Galton Board
2023-06-13 Update README.md
    circuit board chapter
2023-06-13 add stl files in text
2023-06-13 stl files marble pump
2023-06-13 fix Event object decleration
    [laser_sensor.py]
2023-06-13 corner stl
2023-06-13 laser alignment
2023-06-13 switching subsections
